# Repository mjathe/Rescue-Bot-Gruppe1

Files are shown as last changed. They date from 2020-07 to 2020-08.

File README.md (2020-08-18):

# Rettungsroboter - Projekt angewandte Elektrotechnik
Wenn Menschen an gefährlichen Orten verunfallen. müssen diese gerettet werden. Manchmal ist die Situation so gefährlich, dass eine erhöhte Gefahr für den Rettenden nicht ausgeschlossen werden kann. In solchen Situation ist es sinnvoll Rettungsroboter einzusetzen.

Im Rahmen dieses Projekts soll ein Rettungsroboter entwickelt werden, welcher sich autonom in einer festgelegten Umgebung bewegen kann.
## Projektmanagement
[Trello](https://trello.com/b/rEBa2gHf/rescue-bot-group-1)

## Szenario
Das Szenario ist ein Waldbrand. Der Roboter wird an einer bestimmten Stelle ausgesetzt und soll sich autonom zu der zu rettenden Person navigieren. Für die Selbstbehandlung der Person, trägt der Roboter ein Erste-Hilfe-Kit mit sich. Außerdem soll bei der Person ein blaues Rauchsignal gezündet werden, damit ein Rettungsteam den Standort bestimmen kann. Für die Kommunikation zwischen Rettungsteam und der Person besitzt der Roboter eine Gegensprechanlage.

## Requirements
| ID |Description  |
|--|--|
|  FR A|Der Roboter muss autonom fahren können.  |
| FR A.1|Der Roboter muss auf dem Land fahren können.|
|NFR A.1.1 | Der Roboter soll auf Ketten fahren.|
|FR A.2|Der Roboter muss auf dem Wasser fahren können.|
|FR A.2.1|Der Roboter muss schwimmen können.|
|FR A.2.2|Der Roboter muss wasserfest sein.|
|NFR A.2.3|An den Ketten befinden sich Paddelbleche für die Bewegung im Wasser.|
|FR A.3|Der Roboter muss Hindernissen ausweichen können.|
|FR A.3.1|Der Roboter muss Hindernisse erkennen.|
|FR B|Der Roboter muss einen Erste-Hilfe-Kasten tragen können.|
|FR C|Der Roboter muss Schallsignale erkennen und differenzieren können.|
|FR C.1|Der Roboter muss Schallsiganle in der Ebene aus allen 4 Richtungen erkennen.|
|FR D|Der Roboter muss das zu retten Objekt identifizieren können.|
|FR D.1|Der Roboter muss die Temperatur des Objekts bestimmen können.|
|FR D.2|Die Temperatur soll über eine Wärmebildkamera bestimmt werden.|
|FR E|Der Roboter soll eine Gegensprechanlage besitzen.|
|FR F|Der Roboter muss sich bei größerer Beladung für den Landweg entscheiden.|

## Kontextdiagramm

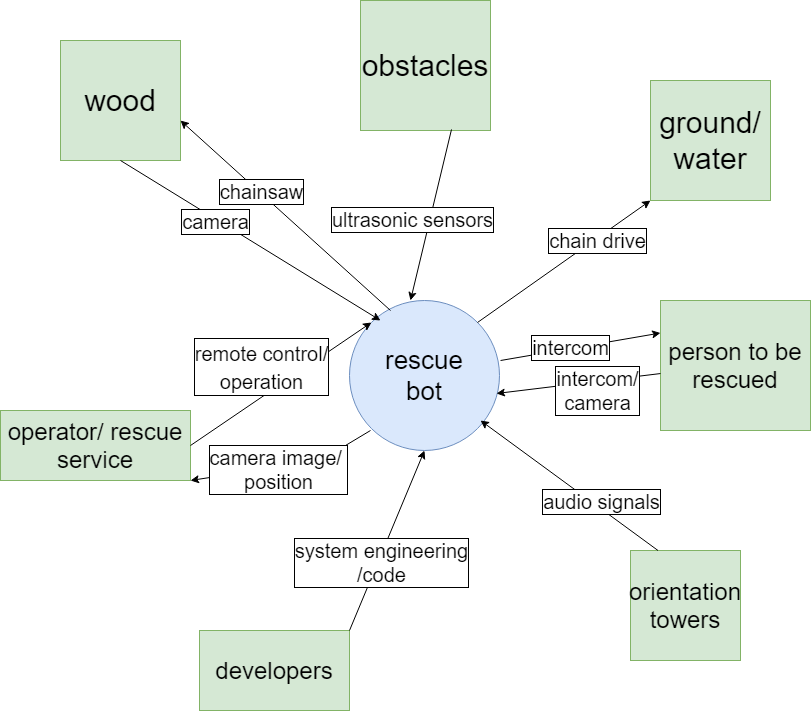
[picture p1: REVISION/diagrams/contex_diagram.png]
Kontextdiagramm


## Use Case Diagram

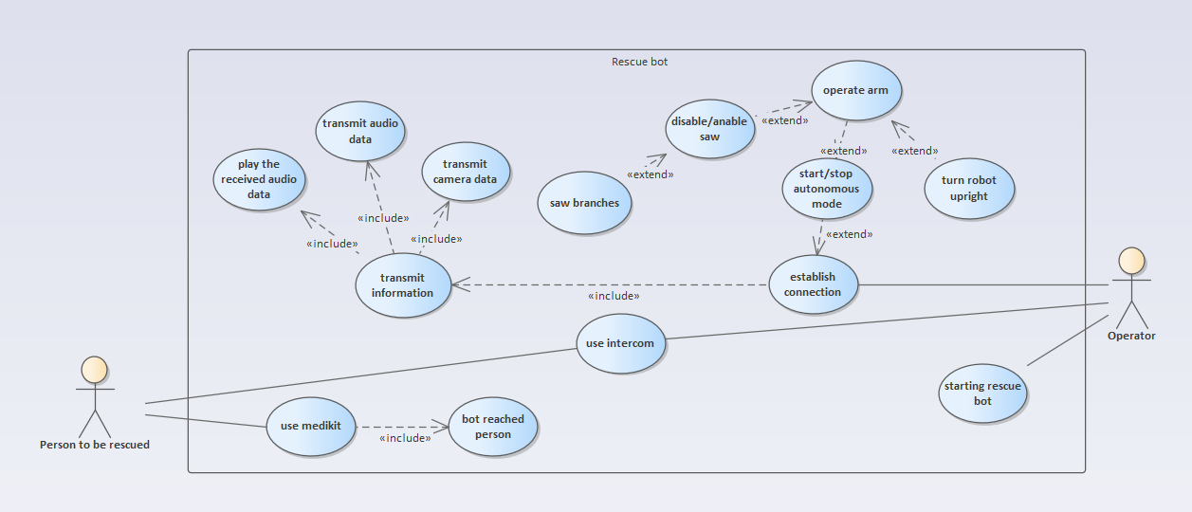
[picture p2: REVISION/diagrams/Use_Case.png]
Use Case Diagram


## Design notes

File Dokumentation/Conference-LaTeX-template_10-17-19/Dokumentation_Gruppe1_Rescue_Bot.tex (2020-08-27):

\documentclass[conference]{IEEEtran}
\IEEEoverridecommandlockouts
% The preceding line is only needed to identify funding in the first footnote. If that is unneeded, please comment it out.
\usepackage{cite}
\usepackage{amsmath,amssymb,amsfonts}
\usepackage{algorithmic}
\usepackage{graphicx}
\usepackage{textcomp}
\usepackage{xcolor}
\def\BibTeX{{\rm B\kern-.05em{\sc i\kern-.025em b}\kern-.08em
    T\kern-.1667em\lower.7ex\hbox{E}\kern-.125emX}}
\begin{document}

\title{Conference Paper Title*\\
{\footnotesize \textsuperscript{*}Note: Sub-titles are not captured in Xplore and
should not be used}
\thanks{Identify applicable funding agency here. If none, delete this.}
}

\author{\IEEEauthorblockN{ Benedikt Lipinski}
\IEEEauthorblockA{\textit{Hochschule Hamm- Lippstadt} \\
Soest,Germany \\
benedikt.lipinski@stud.hshl.de}
\and
\IEEEauthorblockN{ Jonas Gerken}
\IEEEauthorblockA{\textit{dept. name of organization (of Aff.)} \\
\textit{name of organization (of Aff.)}\\
City, Country \\
email address or ORCID}
\and
\IEEEauthorblockN{ Michael Jathe}
\IEEEauthorblockA{\textit{dept. name of organization (of Aff.)} \\
\textit{name of organization (of Aff.)}\\
City, Country \\
email address or ORCID}
\and
\IEEEauthorblockN{ Niklas Heiber}
\IEEEauthorblockA{\textit{dept. name of organization (of Aff.)} \\
\textit{name of organization (of Aff.)}\\
City, Country \\
email address or ORCID}

}

\maketitle

\begin{center}
\begin{abstract}
This document is a model and instructions for \LaTeX.
This and the IEEEtran.cls file define the components of your paper [title, text, heads, etc.]. *CRITICAL: Do Not Use Symbols, Special Characters, Footnotes, 
or Math in Paper Title or Abstract.
\end{abstract}
\end{center}
\titlepage

\section{Motivation (BL)}
In Katastrophenlagen und Ausnahmesituationen können für Menschen oft lebensbedrohliche Bedingungen herrschen. So, dass es im Einsatz von Rettungskräften nicht selten zu gefährlichen Momenten kommt, in denen die eigentlich zur Hilfe eingesetzten Kräfte, selbst zu Hilfe-Ersuchenden werden. \par
Ein Einsatzszenario, in dem Verletzungen, oft schwerwiegend sind, ist die Bedrohung durch Waldbrände. Das Risiko für Einsatzkräfte, sich bei einem Waldbrand zu verletzten, steigt mit jedem brennenden Hektar an Fläche deutlich an. So zeigte sich hier in den letzten 2 Jahren ein starker Anstieg an brennender Fläche mit zuletzt im Jahr 2019 2.711 ha Fläche \cite[S.7B1]{stat1}. Da ein Anstieg an brennender Fläche nicht nur ein erhöhtes Verletzungsrisiko, sondern auch erschwerte Bedingungen an die Einsatzdurchführung selbst stellt. \par
Da der Schutz von Menschenleben und Einsatzkräften an oberste Stelle steht, aber die Bedingungen in einem Waldbrandeinsatz nicht immer den gedankenlosen Einsatz von menschlichem Personal zulassen, sind die rettenden Einheiten auf technische Lösungen angewiesen, die zu ihrem Schutz und ihrer Unterstützung beitragen.\par 
Zur schnelleren Rettung von vermissten Personen und gleichzeitigem Selbstschutz von Einsatzkräften wird ein technisches Gerät benötigt, das verletzte Personen in einem Waldbrandgebiet aufsuchen kann und somit eine Rettung der Person ohne Gefahr für dritte bezweckt. 
Entwickelt werden soll ein Prototyp, der automatisiert und selbständig eine verletzte Person in einer vorgegeben Umgebung aufspüren kann(A). Der Roboter kann sowohl über Land, wie auch über Wasser zu seinem Ziel gelangen(A1,A2), was ihm mittels eines Kettenantriebes ermöglicht wird(A1.1). Damit das Fahren auf dem Wasser möglich ist, werden an den Laufwerken einzelne Kettenglieder zu Paddelblechen geformt (A2.3)
Um sich selbstständig in seiner Umgebung zurechtfinden zu können, muss der Roboter Hindernisse erkennen und ihnen ausweichen können(A3,A3.1).
\par Um sich im Gelände orientieren zu können, navigiert sich der Roboter indem er auf ein spezifisch codiertes Schall-Signal von bis zu 4 Türmen reagieren kann (C, C.1)
In der Interaktion mit einem potentiellen Waldbrandopfer soll das Fahrzeug einen Ersthilfekasten bei sich tragen(B), um der gefundenen Person zu ermöglichen, kleinere Verletzungen bei sich selbst zu behandeln. Zudem sollen Temperaturen von Objekten bestimmt werden können, damit die eines Menschen so wie auch die Temperatur des zu befahrenen Bereichs bestimmt werden kann ( D.1). Des Weiteren kann die verletzte Person mittels einer Gegensprechanlage Kontakt mit dem Rettungspersonal aufnehmen(E). Eine weitere- jedoch verworfene- Anforderung ist die Entscheidung für einen Landweg, sollte das Fahrzeug zu schwer gelastet sein. Jedoch sind im Projektverlauf weitere Anforderungen hinzu gekommen, zum Beispiel wäre das die Umsetzung einer vom Operator per Fernbedienung gesteuerten Kettensäge auf dem Roboter. Diese Funktion soll eine bessere Fortbewegung im Gelände ermöglichen.
\par Die Anforderungen wurden durch die komplette Gruppe anhand des durch die Aufgabe festgelegten Rahmens erstellt.

\begin{figure}[h] 
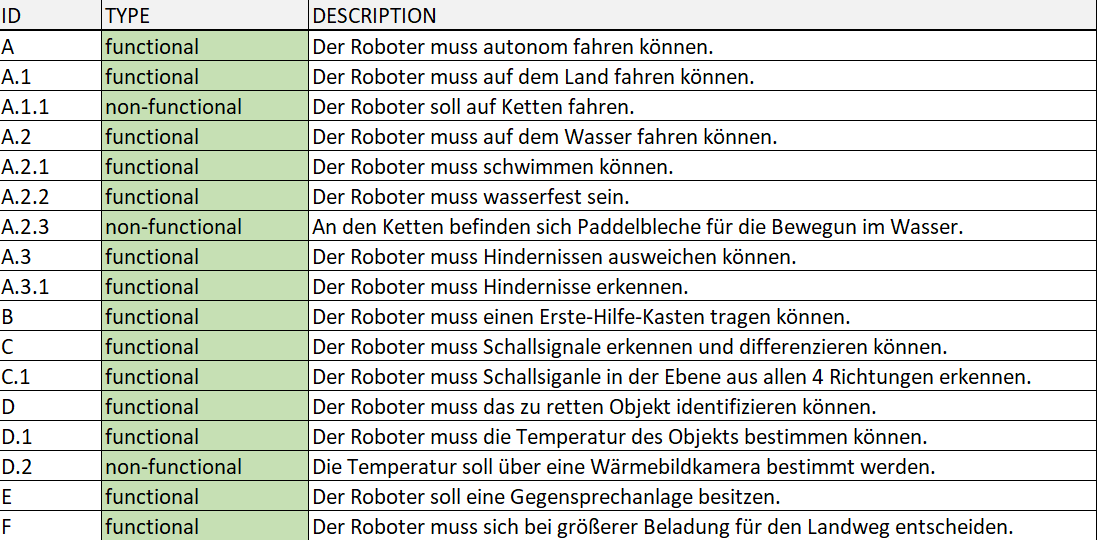
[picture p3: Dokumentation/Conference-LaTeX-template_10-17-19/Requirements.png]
\center{}
\caption{Anforderungsliste }
\label{fig.1}
\end{figure}

\section{Implementation des Roboters (BL)}
{
Als letzten Schritt vor der finalen Umsetzung in wirklichen Programmiercode wurden die abgeleiteten Algorithmen beispielhaft ohne jegliche reale Syntax Umgesetzt. Die diente zum besseren Verständnis der späteren Übersetzung der Algorithmen von der Beschreibung durch Diagramme in die Beschreibung durch von Maschinen lesbare Sprache. Ziel war es zudem, nicht nur einem Compiler die Lesbarkeit zu ermöglichen, sondern auch die Abstimmung in der Gruppe, um zu gewährleisten, dass der durch mich abgeleitete Code, auch den übrigen Gruppenmitgliedern in der Form schlüssig erschien und nicht durch ein Verständnisproblem in eine falsche Richtung entwickelt wurde. Ein positiver Nebeneffekt ist zudem, dass sich bereits nach der Umsetzung in Pseudo-Code mögliche Unstimmigkeiten in Schnittstellen aufgetan hätten, aber auch die Arbeit von mehr als einer Person in der weiteren Umsetzung nicht die Gefahr gebracht hätte, Fehler zu erzeugen. \par
Die Entscheidung, in welcher Programmiersprache der Roboter umgesetzt wird, fiel auf C++. Die Gründe für die Auswahl ergeben sich daraus, dass Programme in C++ leicht zu verstehen und auch umzusetzen sind. Das bedeutet, die Programmierung war für alle Teilnehmer in der Gruppe ohne Probleme möglich, da bereits im Verlauf des Studiums alle Mitglieder mehrfach durch die Arduino-Programmierung im Rahmen von Projekten zu tun hatten und somit nicht erst eine neue Sprache zu erlernen hatten. Weitere Vorteile von C++ sind, dass die Sprache in ihrem Kern recht schlank ist, und somit sehr schlank ist. Auf Funktionen muss allerdings nicht verzichtet werden, da eine große Anzahl an Bibliotheken zur Verfügung steht, die bei Bedarf mit eingebunden werden können. Letzter Entscheidungsgrund für C++ ist der Schlankheit der Sprache geschuldet. Entscheidend war der Faktor, dass C++ auf einer hohen Anzahl an Umgebungen zur Verfügung steht. Beispiele wären der bereits erwähnte Arduino, der sich besonders für das Entwickeln von Prototypen eignet. Ein weiteres Beispiel sind Microsoft Windows Betriebssysteme, in denen mit einem C++ Compiler und den Entwicklungsumgebungen von zum Beispiel  Visual Studio oder Eclipse sehr komfortabel Quellcode in C++ entwickelt werden kann.\par 
Zu den aktuellen Bestandteilen des Systems, die in Programmiercode umgesetzt wurden, zählen die elementaren Bestandteile der selbständigen Fahrt zu einer verunfallten Person in einem Testszenario. Genauer wurde die Entscheidung umgesetzt, ob ein Fahrzeug sich zum Zeitpunkt auf dem Landweg, oder auf dem Wasser befindet. Des weiteren wurde Wert auf die Navigation per Schallsendeturm gelegt und implementiert. Der Prototyp kann zudem voll automatisch auf die Türme ausrichten und die Motoren ansteuern. Zu diesem Zeitpunkt wurde die folgende Liste an Klassen implementiert: 

Alignment.hpp, in der die Ausrichtung des Fahrzeugs auf Basis der Navigationsdaten der AudioNavigation in Grad eingestellt wird. Dementsprechend wird in der AudioNavigation.hpp Steueranweisung für das Ausrichten berechnet. Für diesen Schritt müssen Informationen von den Audiosendetürmen vorliegen. 
Die Entscheidung ob sich das Fahrzeug im Wassermodus bewegt, oder ob der Landmodus festgelegt ist, wird im DriveMode.hpp eingestellt. Aufgerufen werden diese Klassen durch die MainControl.hpp fortlaufen, solange bis ein Operator die autonome Fahrweise des Roboters unterbrechen sollte. Des weiteren wird die Umgebung des Fahrzeugs auf Hindernisse überprüft, was mittels ObjectDetection.hpp implementiert wurde.
Nach einem positiven Befund der ObjectDetection.hpp wird aufgrund der festgelegten Requirements des Projektes noch ein weiterer Schritt notwendig, der in der ObstacleDetection.hpp zum jetzigen Zeitpunkt( 26.08.2020) nur angedeutet wurde. Bei diesem schritt handelt es sich um die Unterscheidung eines nicht näher bekannten Objekts, in dem Falle ein Hindernisse, oder der Entscheidung zwischen einem der beiden bekannten Objekte, die sich aus der Kategorie Äste und der Kategorie Personen ergeben.

Zudem wurde die Kommunikation mit den Sensoren über die SensorController.hpp umgesetzt, aber auch die Ansteuerung des Laufwerksmotors wurde mit der MotorControl.hpp implementiert
\par
Als sehr wichtigen Bestandteil des Projektes stellt sich die Implementation der AudioNavigation heraus, die im Folgenden genauer beschrieben wird.
\par
\textit{Alignment.hpp}\\
Damit eine zuverlässige Navigation durch die Testumgebung stattfinden kann ist es für das Fahrzeug notwendig, die Richtung in die der Roboter zu fahren hat herausfinden kann, dazu benötigt er eine kleine Hilfestellungen durch auf dem Gelände montierte Schallsignal gebende Türme, deren Position bekannt ist.
Durch diese Navigationshilfe und die Bekanntheit der Strecken kann das Fahrzeug entscheiden, wie es sich zu verhalten hat.
\par 
In der Erweiterung, die die Alignment.hpp dem Roboter zur Verfügung stellt, kann der Rescue-Roboter sich basierend auf dem Nordpol der Karte und seiner eigenen Differenz dazu ermitteln, um wie viel Grad er sich drehen muss, um in Richtung des Sendeturms ausgerichtet zu sein. Hierbei hilft ihm die Codierung des Turms und die Differenz der Ausrichtung, die mittels Signalen eines Kompass ermittelt werden kann. Implementiert ist dies durch zwei Klassen mit einer steuernden Funktion: \textcolor{teal}{adjustAlignment} deren Aufgabe darin besteht zum einen, die Rechnung zu Differezberechnung \textcolor{teal}{differenceAlignment} aufzurufen, und zum zweiten das Ergebnis an die Motoren weiter zu geben. Die Formel für die Differenz wird errechnet aus der $differenz =gewünschtenAusrichtung - aktuellenAusrichtung $. Die gewünschte Ausrichtung wird durch den Aufruf aus der Klasse  AudioNavigation mit übergeben.\par
\par
\textit{AudioNavigation.hpp}
\par
Genauer wird die gewünschte Ausrichtung in der Methode \textcolor{teal}{Navigate} der Klasse AudiNavigation festgelegt. Basierend auf der Information welcher Turm ein positives Signal gegeben hat, kann in der Navigationsklasse entschieden werden in welche Richtung sich gedreht werden soll. 
Dazu ist bekannt, bei welcher Kombination von aktiven Türmen sich in welche Richtung gedreht werden muss. Ein Beispiel dazu: sollte  $checkForAudioSignals() = {1,0,0,1}$ zurück geben, dann kann das Fahrzeug sich nur am Umkehrpunkt befinden. Die eingestellte Richtung wäre in diesem Fall 90° im Verhältnis zum Nordpol der Karte, das Fahrzeug würde Richtung Osten fahren-  auf Turm 4 zu. Der Grund für die Entscheidung besteht darin, dass die strecke vom Start bis zum Turm 4 die kürzeste Strecke zum Patienten ist. 
\par
\textit{SensorController.hpp}
\par
Die für die Streckenwahl notwendigen Informationen lassen sich aus der für den SensorController bestimmten Klasse SensorController abrufen. Die in dem SensorController überwiegend erledigten Aufgaben beziehen sich zu einem sehr großen Teil darauf, Informationen von Sensoren zu erfragen und diese bereits vor der eigentlichen Verarbeitung aufzubereiten. Die Aufbereitung bedeutet zum Beispiel, dass im Falle der Navigation mittels Schall eine Codierung des Schallsignals zur Bestimmung des Startpunktes der Nachricht vor der eigentlichen Nachricht übermittelt wird. Ganz konkret bedeutet das, dass die Nachricht die den Turm 1 beschreibt nicht nur aus $001$, sondern aus jeweils drei vorangestellten HIGH und LOW Bits besteht, demnach $111000001$. Die Informationen ob und welcher Turm erkannt wurde, werden nur in dem Fall zurückgegeben, wenn diese Codierung korrekt abgeglichen werden konnte.
Des weiteren behandelt der Sensorcontroller die Abfrage der Ultraschallsensoren, der Wassersensoren und des Kompass. Zusammenfassend lässt sich sagen, dass der SensorController einen großen Teil der Schnittstellen mit denen der Rescue-Bot mit seiner Testumgebung interagiert beinhaltet. 
\par

||Die Klasse SensorController.hpp wurde durch "mich" auf der Grundlage von der durch Jonas Gerken erstellten ersten Implementierung des SensorControllers verfeinert. Die weiteren Klassen mit denen das Verhalten des Rescue-Bots umgesetzt wurde, sind zusammengerechnet ca. 30h Zeit. ||
\par 

Die Umsetzung des Projektes beinhaltet, neben der Implementierung eines Rettungsroboters, auch die Simulation einer Umgebung in der sich der Roboter bewegen soll. Das beinhaltet neben der Umgebung selbst auch die Interaktion mit dieser simulierten Umgebung.

}

\begin{IEEEkeywords}
component, formatting, style, styling, insert
\end{IEEEkeywords}
\bibitem{stat1} Bundesanstalt für Landwirtschaft und Ernährung,Waldbrandstatistik der Bundesrepublik Deutschland für das Jahr 2019, Statista,Veröffentlichung 25.06.2020, Waldbrand statistik-b.pdf, Letzter Abruf 25.08.2020

\begin{thebibliography}{00}

\end{thebibliography}
\vspace{12pt}
\end{document}

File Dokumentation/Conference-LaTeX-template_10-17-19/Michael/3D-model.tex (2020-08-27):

\begin{figure}[h]
    \centering
    \captionsetup{width=.9\linewidth}
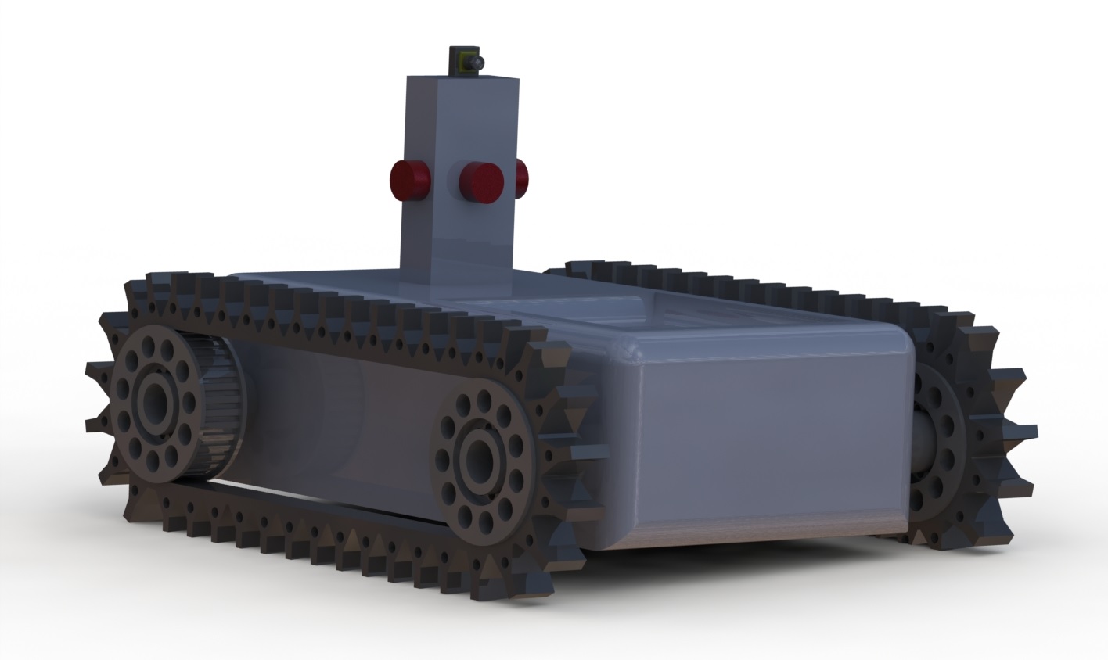
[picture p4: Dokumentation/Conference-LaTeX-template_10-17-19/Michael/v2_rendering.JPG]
    
    \caption{Erster Prototyp}
    \label{fig:prot}
\end{figure}

Das 3D-Modell des Rettungsroboters wurde mit der Software SolidWorks erstellt. Die Abbildung \ref{fig:prot} zeigt den ersten Prototyp. Hier wurden schon der Kettenantrieb und eine Ablagefläche für ein Erste-Hilfe-Kit umgesetzt. Weiter wurde auf dem Robotor ein Turm platziert, um dort 4 Sensroen für die Orientierung anzubringen. Oben auf dem Turm befindet sich eine Kamera.\\

\begin{figure}[h]
    \centering
    \captionsetup{width=.9\linewidth}
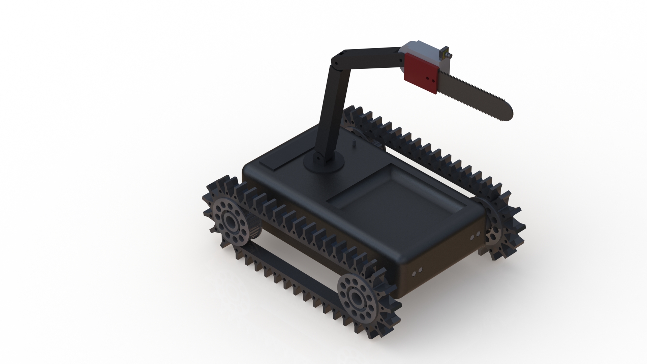
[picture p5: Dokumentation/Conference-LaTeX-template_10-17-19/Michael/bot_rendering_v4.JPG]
    
    \caption{Zweite Version des Roboters}
    \label{fig:second}
\end{figure}

Für die zweite Version des Prototyps wurde zunächst der Körper des Bots angepasst. Für eine Verbesserung des Strömungsverhaltens und einer Erhöhung des Böschungswinkels wurde der Körper an der vorderen unteren Kante mit einer sehr flachen Fase versehen.

Im nächsten Schritt wurde der unbewegliche Turm durch einen Roboterarm mit 3 Gelenken und einer Drehscheibe ersetzt (Abb. \ref{fig:second}). Am Ende des Arms wurde eine Kettensäge angebracht. Die Kamera wurde auf der Säge angebracht, um so die Säge immer im Blick zu haben.

Weiter wurden noch ein austauschbarer Akku, ein omnidirektionales Mikrofon und Ultraschallsensoren in den Prototyp intgeriert.\\
\begin{figure}[h]
    \centering
    \captionsetup{width=.9\linewidth}
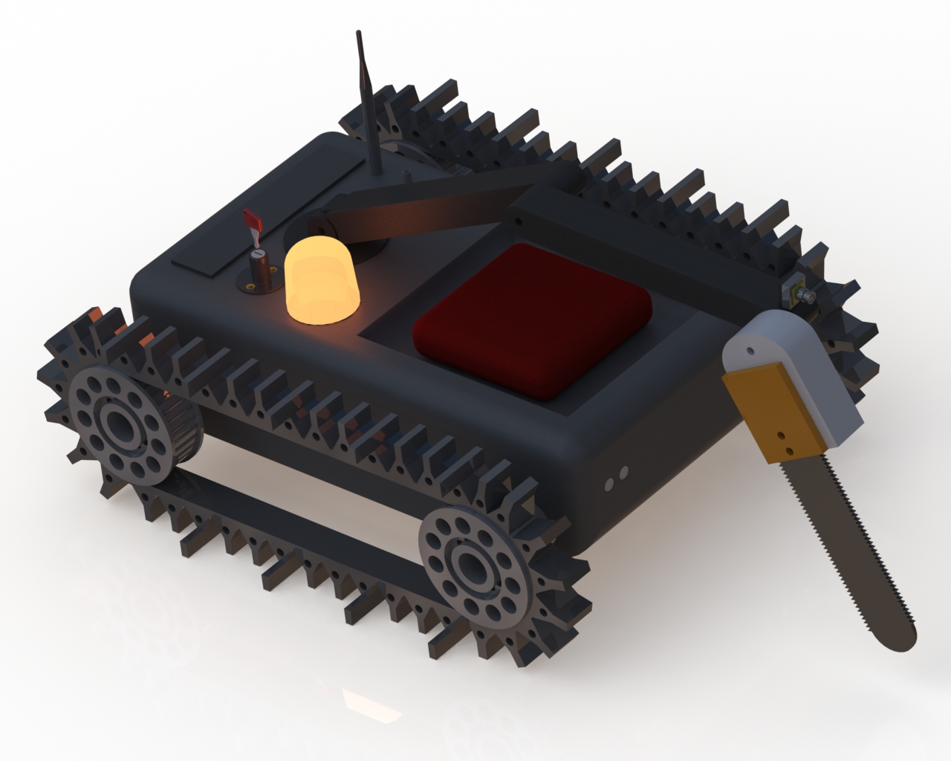
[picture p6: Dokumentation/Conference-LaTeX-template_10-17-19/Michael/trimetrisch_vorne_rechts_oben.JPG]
    
    \caption{Außenansicht des finalen Roboters}
    \label{fig:final}
\end{figure}
Abbildung \ref{fig:context} zeigt das finale Modell. Im Vergleich  zur vorherigen Version noch folgende Elemente hinzugefügt:
\begin{itemize}
    \item Rundumleuchte
    \item Antenne
    \item Ein/Aus-Schalter
    \item seitliche Paddel an den Ketten\\
\end{itemize}

Der komplette Arm des Roboters hat eine Revision erfahren, so dass die beiden Teilarme und die Säge eingeklappt werden können. Die Kamera wurde auf den oberen Arm versetzt, damit die Kettensäge eingeklappt werden kann und der Operator trotzdem die Sicht nach Vorn behält.

Außerdem wurde der Hauptkörper des Roboters in eine Wanne und einen Deckel unterteilt, um zum Einen die Teile druckbar zu machen und zum ist nur so möglich die benötigte Hardware (Motoren, Mikrocontroller, usw.) zu installieren.  \\

Die Abbildungen \ref{fig:top} und \ref{fig:front} zeigen, dass für die vorgesehene Hardware genug Platz vorhanden ist und auch entsprechende Befestigungspunkte vorhanden sind.\\
\begin{figure}[h]
    \centering
    \captionsetup{width=.9\linewidth}
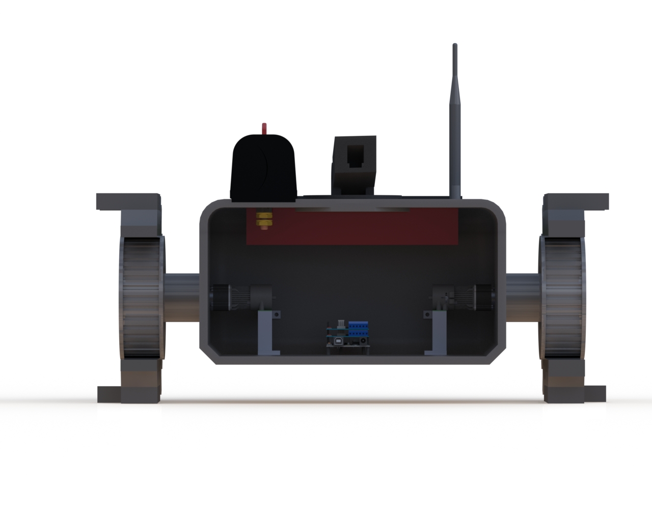
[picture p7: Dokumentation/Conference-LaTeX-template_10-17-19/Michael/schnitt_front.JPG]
    
    \caption{Schnittansicht von vorne}
    \label{fig:front}
\end{figure}\\
\begin{figure}[h]
    \centering
    \captionsetup{width=.9\linewidth}
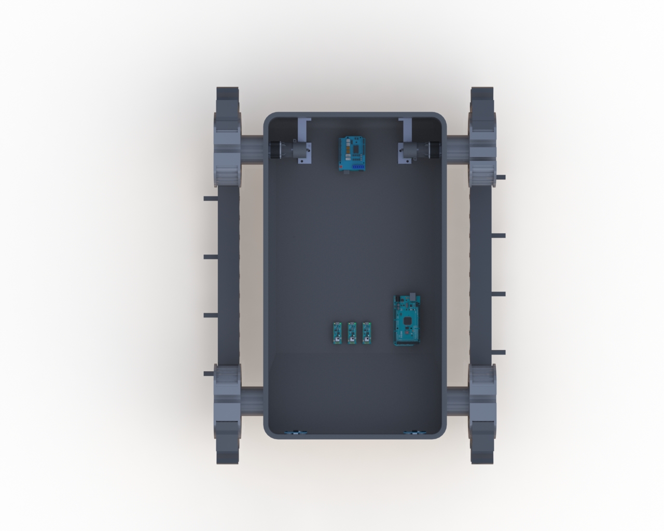
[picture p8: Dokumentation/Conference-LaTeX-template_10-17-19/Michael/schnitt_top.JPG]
    
    \caption{Schnittansicht von oben}
    \label{fig:top}
\end{figure}\\
Zum Schluss wurden alle Druckteile mit Hilfe des Felix Repetier Hosts auf Druckbarkeit überprüft. Abbildung \ref{fig:print_stats} zeigt die Statistiken für einen 3D-Druck mit 25\% Infill  und ABS Filament. Aus der benötigten Filamentmenge und der spezifischen Materialdichte lässt sich das Gewicht der Druckteile errechnen (Abb. \ref{fig:filament_weight}). Hier ergibt sich ein Gewicht von etwa 5,67 kg.

In Solidworks wurde für die Wanne des Hauptkörpers ein Volumen von etwa 7,9 Liter berechnet. Daraus lässt sich schließen, dass der Roboter ein Gesamtgewicht von 7,9 kg nicht überschreiten sollte. Da die Druckteile schon 5,67 kg  wiegen, bleiben für die restlichen Teile (Motoren, Akku, Elektronik, Säge, Lager, Erste-Hilfe-Kit) nur etwa 2,23 kg.
Das wäre nicht sinngemäß zu realisieren. Das bedeutet der Hauptkörper sollte noch deutlich vergrößert werden. Zusätzlich könnten die Wandstärken verringert werden, um Gewicht zu Sparen. Für die Teile des Roboterarms würde sich ein Fachwerk anbieten. 
\begin{figure}[h]
    \centering
    \captionsetup{width=.9\linewidth}
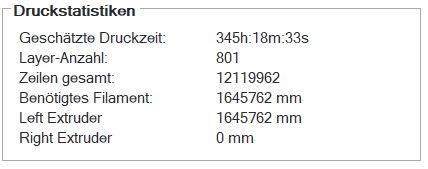
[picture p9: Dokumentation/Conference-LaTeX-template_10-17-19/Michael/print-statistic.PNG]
    
    \caption{Druckstatistiken}
    \label{fig:print_stats}
\end{figure}
\begin{figure}[h]
    \centering
    \captionsetup{width=.9\linewidth}
    
    \caption{Erechnetes Filamentgewicht}
    \label{fig:filament_weight}
\end{figure}

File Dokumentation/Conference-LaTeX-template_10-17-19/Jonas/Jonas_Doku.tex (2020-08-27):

\documentclass[conference]{IEEEtran}
\IEEEoverridecommandlockouts
% The preceding line is only needed to identify funding in the first footnote. If that is unneeded, please comment it out.
\usepackage{cite}
\usepackage{amsmath,amssymb,amsfonts}
\usepackage{algorithmic}
\usepackage{graphicx}
\usepackage{textcomp}
\usepackage{xcolor}
\def\BibTeX{{\rm B\kern-.05em{\sc i\kern-.025em b}\kern-.08em
    T\kern-.1667em\lower.7ex\hbox{E}\kern-.125emX}}
\begin{document}

\title{PAE Gruppe 1*\\
{\footnotesize \textsuperscript{*}Note: Sub-titles are not captured in Xplore and
should not be used}
\thanks{Identify applicable funding agency here. If none, delete this.}
}

\author{\IEEEauthorblockN{1\textsuperscript{st} Given Name Surname}
\IEEEauthorblockA{\textit{dept. name of organization (of Aff.)} \\
\textit{name of organization (of Aff.)}\\
City, Country \\
email address or ORCID}
\and
\IEEEauthorblockN{2\textsuperscript{nd} Given Name Surname}
\IEEEauthorblockA{\textit{dept. name of organization (of Aff.)} \\
\textit{name of organization (of Aff.)}\\
City, Country \\
email address or ORCID}
\and
\IEEEauthorblockN{3\textsuperscript{rd} Given Name Surname}
\IEEEauthorblockA{\textit{dept. name of organization (of Aff.)} \\
\textit{name of organization (of Aff.)}\\
City, Country \\
email address or ORCID}
\and
\IEEEauthorblockN{4\textsuperscript{th} Given Name Surname}
\IEEEauthorblockA{\textit{dept. name of organization (of Aff.)} \\
\textit{name of organization (of Aff.)}\\
City, Country \\
email address or ORCID}
}

\maketitle

\begin{abstract}

\end{abstract}

\section{Use Case (JG)}

\begin{figure}[htbp]
	\centering
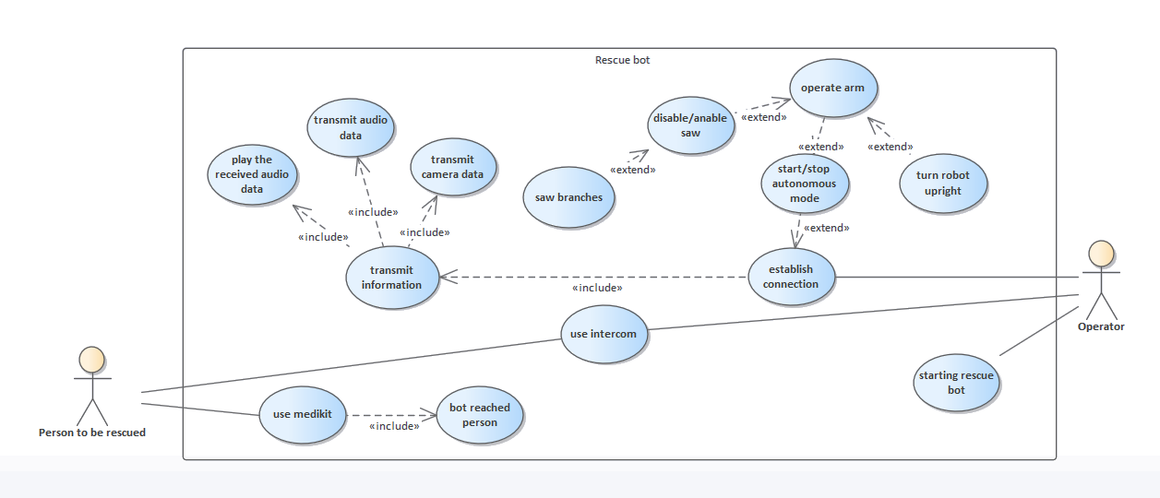
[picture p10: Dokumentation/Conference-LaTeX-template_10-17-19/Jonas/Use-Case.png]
	
	\caption{Use Case}
\end{figure}

Nach der Erstellung der Anforderungen haben wir ein Use Case Diagramm erstellt.\newline 
In Fig. 1 ist das Use Case Diagramm zusehen. Außerhalb stehen die Aktoren "Operator" und "Person to be rescued", als Strichmännchen dargestellt. Innerhalb sind die Funktionen des rescue bots dargestellt und wie diese mit den Aktoren verbunden sind. Die Use Cases sind mit inludes oder extends untereinander verbunden. Die Aktoren sind durch Assoziationen mit den Use Cases verbunden. Zum Beispiel kann der Operator den rescue bot starten. Dann stellt der Operator eine Verbindung mit dem rescue bot her. Über die Verbindung zum rescue bot werden verschiedene Informationen, wie Kamera Daten und Audio Daten übermittelt. Der Operator kann zwischen Autonomen und manuellen Modus wechseln. Im manuellen Modus kann der Operator den Arm bedienen. Zudem kann er eine Säge aktivieren oder deaktivieren um Äste zu durchsägen.
Der Arm kann auch dafür benutzt werden, den rescue bot wieder aufzustellen wenn er auf die Seite gefallen ist.
Wenn der rescue bot die zu rettende Person erreicht hat, kann der Operator über eine Gegensprechanlage die Person ansprechen. Zum schluss kann die zu rettende Person ein medikit benutzen, um selbst kleine Verletzungen zu versorgen.

\section{Stakeholder (JG)}
Um mögliche Risiken oder Blockaden, die das Projekt stoppen oder zum Abbruch bringen können zu finden haben wir eine Stakeholderanalyse durchgeführt. Stakeholder sind alle Personen, die mit dem Projekt in Kontakt kommen. Dazu gehören z.B. der Arbeitgeber, das Rettungsteam, die zu rettende Person (Opfer), Finanzmanager und der TÜV.
\\

\subsection{Rettungshelfer}
Die Rettungshelfer wollen sich selbst und dritte nicht zusätzlich in gefährlichen Situationen in Gefahr bringen.
Die Lösung dafür ist, das der Roboter anwendbar für Situationen die zu Gefährlich für die Rettungshelfer sind gemacht wird.

\subsection{Menschen die gerettet werden}

Die zu rettenden Menschen wollen eine schnelle medizinische Hilfe und schnelle Rettung.
Hier ist die Lösung, das der zu rettende Mensch so schnell und sanft wie möglich gerettet wird.

\subsection{Familie des zu rettenden Menschen}

Die Familie des zu rettenden Menschen will wissen, das ihre Verwandtschaft in Sicherheit ist.
Um der Familie dies zu bieten, muss dem zu rettenden Menschen die best mögliche Rettung geliefert werden.

\subsection{Finanzmanager}

Der Finazminister will ein Produkt mit einem hohen Mehrwert zu möglichst niedrigen kosten.
Dazu ist die Lösung, ein System mit einem guten Preis-Leistungsverhältnis zu entwickeln.

\subsection{Arbeitgeber}

Der Arbeitgeber möchte ein verkaufbares Prokdut mit einer hohen verkaufsrate und einem hohen Profit.
Die Lösung ist, eine System mit hoher Sicherheit aufzubauen, um eine Entschädigung zu vermeiden und einen Kaufanreiz zu schaffen, der auch mit einem hohen Profit möglich ist.

\subsection{TÜV}

Der TÜV möchte Sicherheit für alle Beteiligten, wie Rettungshelfer, Menschen die gerettet werden sollen und Dritte.
Um dies einzuhalten müssen Richtlinien eingehalten und ein sicheres System eingerichtet werden, um eine TÜV-Zertifizierung zu bekommen. 

\subsection{Kunden}

Der Kunde will, das die Rettungshelfer gut ausgestattet sind.
Dazu wird der rescue bot(Ausstattung) in regelmäßigen abständen gewartet. Zudem gibt es eine Kundenbetreuungen um sie mit dem neuen Produkt vertraut zu machen. Dies ist wichtig um mögliche bedenken zu dem rescue bot beiseite zu schaffen.
\\

\subsection{Stakeholder matrix}

\begin{figure}[htbp]
	\centering
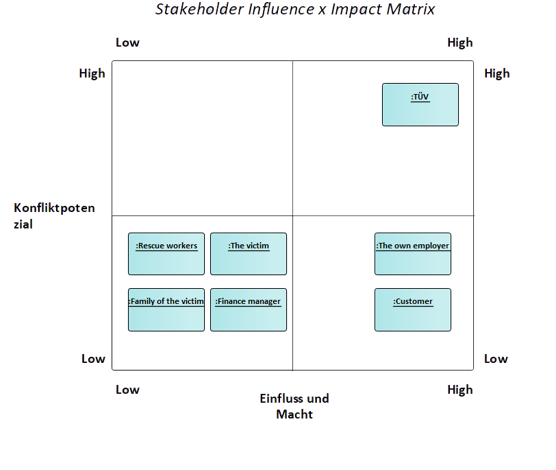
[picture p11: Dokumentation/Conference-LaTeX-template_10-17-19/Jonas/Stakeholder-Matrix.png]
	
	\caption{Stakeholder-Matrix}
\end{figure}

In Fig. 2 ist die Stakeholder-Matrix mit den verschiedenen Stakeholdern zusehen. Die Stakeholder haben wir nach "Einfluss und Macht" und Konfliktpotential sortiert. Die Rettungshelfer, die zu rettende Person, die Familie der zu rettenden Person und der Finanzmanager haben am wenigsten Einfluss und Macht und am wenigsten Konfliktpotenzial in dem Projekt. Diese Stakeholder können kaum bis gar nichts in dem Projekt mit entscheiden. Zum Beispiel will der Finanzmanager ein Produkt mit einem guten Preis-Leistungsverhältnis wie in Kapitel D beschrieben. Was das Projekt am Ende kostet kann der Finanzmanager jedoch nicht beeinflussen. Viel Einfluss aber wenig Konfliktpotential hat der Arbeitgeber und der Kunde. Zum Beispiel kann der Arbeitgeber viel mit entscheiden, was gemacht werden kann und was nicht. Zudem hat der Kunde eine Vorstellung von dem was er will und kann so starken Einfluss auf das Projekt haben. Der TÜV hat ein hohes Konfliktpotenzial und viel Einfluss und Macht. Durch z.B. fehlenden Sicherheitsmaßnahmen kann der TÜV das Projekt zum Abbruch bringen. 

\section{Activity Diagramm (JG)}

Nachdem das Use Case Diagramm erstellt wurde, haben wir ein Aktivitätsdiagramm bezüglich des autonomen Fahrens, wie in Fig. 3 gezeigt, erstellt. Die erste Aktivität ist, das der Operator sich mit dem Rescue bot über das Remotecontroll und dem remote verbindet. Weiter geht es mit der Sensorauslesung und der Evaluierung der Sensordaten. Darüber überprüft er auf Wasser und entscheidet sich bei "water" für über Wasser fahren und bei "no water" für über Land fahren. Die nächste Aktivität ist, das auf Audiosignale überprüft wird. Bei erkanntem Signal folgt der rescue bot dem Signal, ansonsten fährt er gerade aus weiter. Parallel dazu wird die camera über das remote controll aktiviert. Dazu gehören die Aktivitäten send data, receive data und display video. Wenn ein object erkannt wird, wird das Objekt Identifiziert. Ein Objekt wird unterschieden zwischen nicht identifizierbar, identifiziert als sägbares Objekt und identifiziert als Person. Bei einem zersägbaren Objekt wird nachgefragt ob der rescue bot im Autonomen modus ist. Ist der bot nicht im autonomen Modus, wird der bot gestoppt und der remotecontroll (arm/säge) kann verwendet werden. Danach wird abgefragt ob der bot wartet. Wenn ja, dann wird dem rescue bot erlaubt weiter zu fahren. Sollte das Objekt nicht identifizierbar sein, wird es einfach umfahren. Wurde die Person identifiziert, wird abgefragt ob die Person erreicht wurde. Über jeden weg wird abgefragt, ob die Person erreicht wurde. Also nach der Hindernisumfahrung, dem Äste zersägen. Wurde die Person nicht erreicht, werden die Sensoren wieder ausgelesen und so weiter. Wenn sie erreicht wurde, stoppt der rescue bot und der Operator kann mit der Person reden. Zum Schluss fährt der rescue bot zurück.

\begin{figure}[htbp]
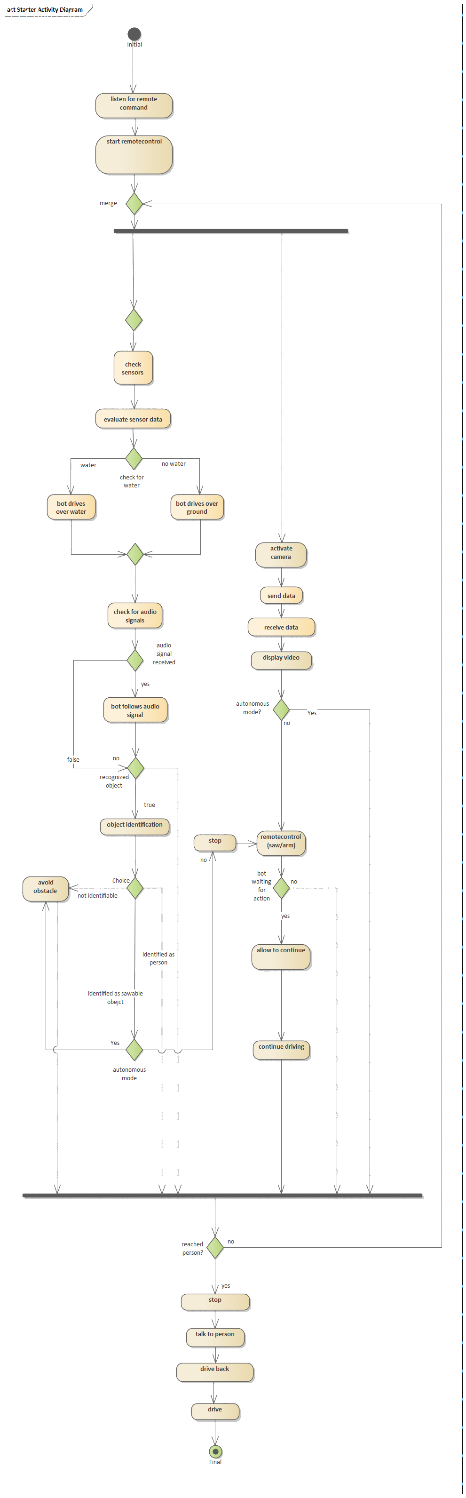
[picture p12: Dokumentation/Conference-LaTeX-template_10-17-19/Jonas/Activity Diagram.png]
	
	\caption{}
	\label{fig:Bild1}
\end{figure}

\newpage

\section{Swimlane (JG)}

In Fig. 4 ist das "Swimlane diagramm" zusehen. Hier wurden die verschiedenen Aktivitäten aus dem Aktivitätsdiagramms nach Sensorcontroller (Blau), Hauptcontroller (Gelb), Motorcontroller (Lila), Objekterkennung (Grün), Remotecontrol (Orange) und remote (Rot) Kategorisiert. Es ist notwendig den rescue bot mit dem remote zu verbinden. Erst danach kann der rescue bot losfahren und die Sensoren auslesen.
Der Sensorcontroller ließt die Sensoren aus und der Hauptcontroller evaluiert sie. Über diese Informationen wird der Motorcontroller angesteuert, ob er auf Land oder Wasser fahren soll. Weiter gibt der Hauptcontroller über empfangene Audiosignale den Befehl, das der rescue bot dem Signal folgen soll. In der Kategorie Objekterkennung unter Objekt Identifizierung wird zwischen nicht identifizierbar, identifiziert als sägbares Objekt und identifiziert als Person unterschieden. Bei einem als zersägbares Objekt identifiziertes Objekt, werden über den Motorcontroller die Motoren gestoppt und der Operator kann über das remote die äste durchsägen. Danach erlaubt der Operator dem rescue bot über die remotesteuerung das weiterfahren. Nachdem die zu rettende Person erreicht wurde, bekommt der Motorcontroller das Signal, die Motoren anzuhalten. Der Operator kann nun über das remote und der Gegensprechanlage mit der zu rettenden Person reden. Am Ende fährt der rescue bot zurück zum Startpunkt.  

\begin{figure}[htbp]
	\centering
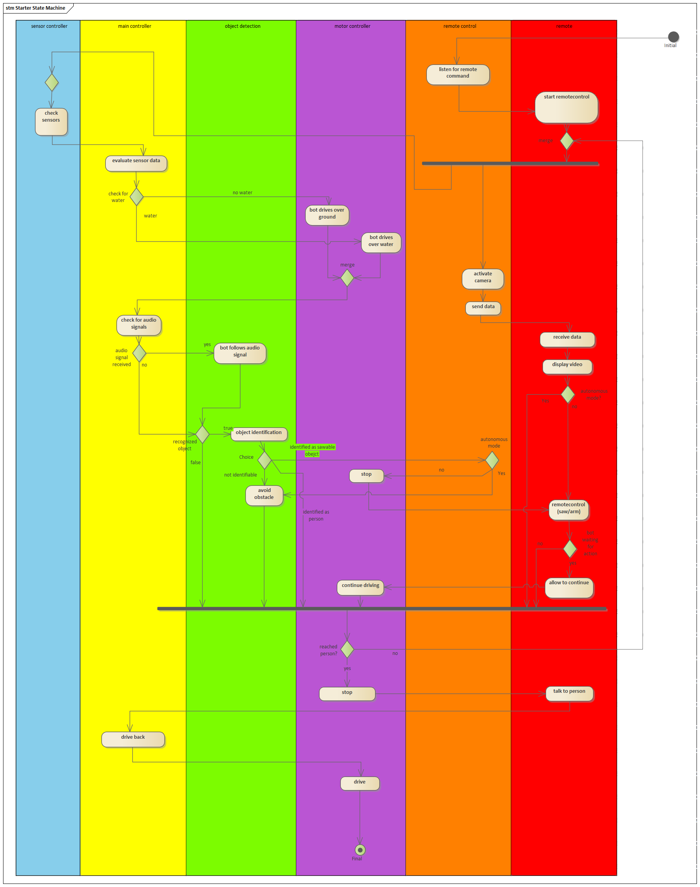
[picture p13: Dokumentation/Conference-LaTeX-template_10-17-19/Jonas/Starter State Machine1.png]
	
	\caption{Swimlane}
	
\end{figure}

\section*{References}

\vspace{12pt}
\color{red}

\end{document}

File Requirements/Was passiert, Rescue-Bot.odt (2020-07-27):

Was passiert, wenn das Feuer bedrohlich wird für Fahrzeug und Objekt ? ?

Es wird ein sprüh-nebel Schutzschild ausgestoßen (ähnl. „Mannschutz“)

Was passiert, wenn die Person eingeklemmt ist ?
aufgrund der Vielfalt der Gegenstände unter denen man eingeklemmt sein könnte stößt das Fahrzeug hier an sein grenzen

Was passiert, wenn der Fluchtweg abgeschnitten ist ?

Das Fahrzeug sucht sich einen anderen weg

Was passiert, wenn das Fahrzeug auf das Dach kippt ?

Durch den (Kettensägen) arm kann das Fahrzeug aufgerichtet werden

Was passiert, wenn das Fahrzeug einen weg um ein Hindernis nicht finden kann ( z.b lange äste ) ?

Das Fahrzeug verfügt über eine kleine Kettensäge

Was passiert, wenn die schleiftrage sich verkantet ?

????? das Fahrzeug setzt andere ende der schleiftrage und versucht sich zu befreien

Was passiert, wenn der Gesundheitszustand der Person sich nicht stabilisiert

?? evtl. per TIVITA wund Erkennung und Hämostatisches mittel

Evtl. Vakuum Matratze mit Beschichter Gold Folie

Ansonsten wenn sich der Zustand nicht verbessert „sofort-Rettung „

Was passiert, wenn die Person zu dick ist um über Wasser zu fahren ?

Der Roboter nimmt den Landweg

- Wenn Fluchtweg abgeschnitten Rettung übers Wasser an Ufernähe ( bestmögliche )

Was passiert, wenn der Roboter bei der Person angekommen ist ?

Per Sprechfunk wird versucht über Kontakter mit der Person in Notlage zu reden

Motor ??
Elektro
DIESEL
Benzin
2Takt

4Takt

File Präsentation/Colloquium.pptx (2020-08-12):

## Colloquium

Gruppe1
Niklas Heiber, Michael Jathe, Jonas Gerken, Benedikt Lipinski

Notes: Benedikt

## Motivation

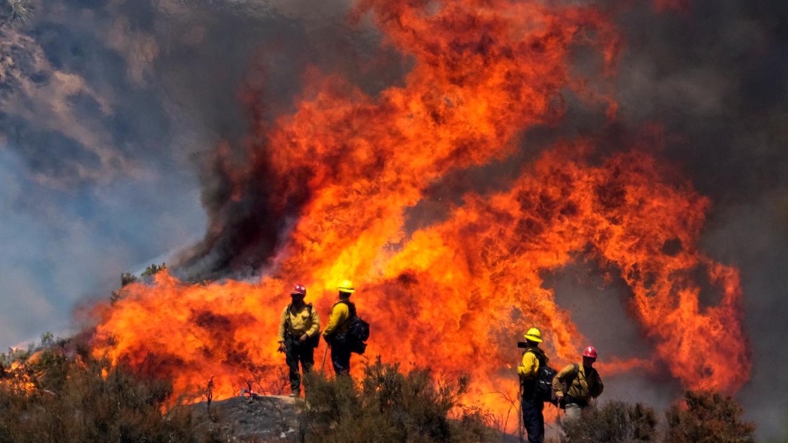
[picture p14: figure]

Einsatz des Bots:
Personen finden und Standort bestimmen
Kommunikation mit den Personen

Szenario: Waldbrand

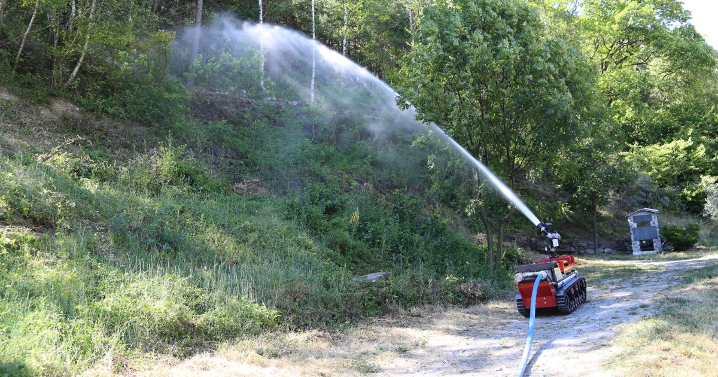
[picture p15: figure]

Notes: Benedikt

## Requirements

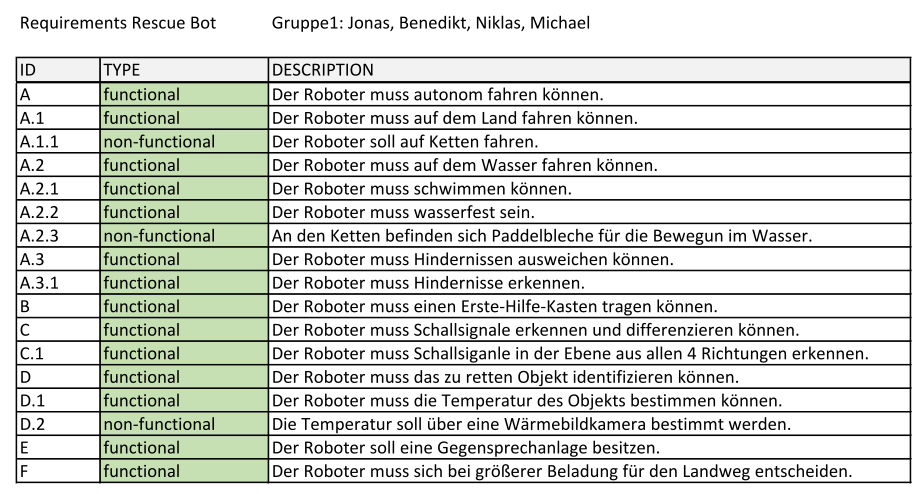
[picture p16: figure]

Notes: Benedikt

## Context modell

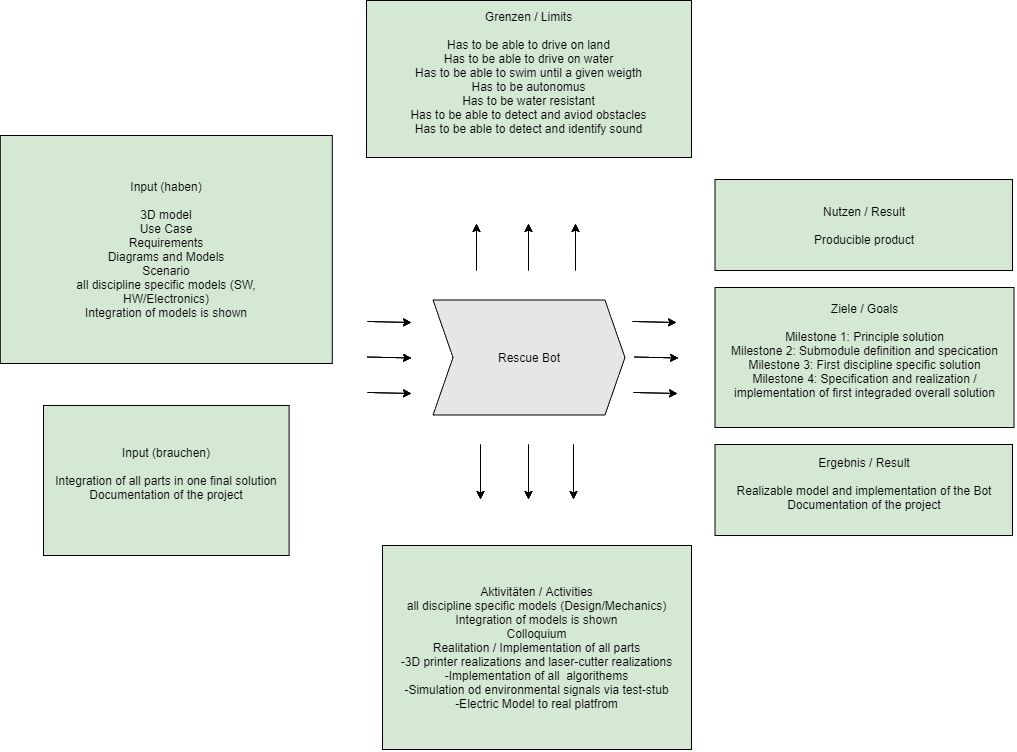
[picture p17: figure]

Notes: Niklas

## Use Case

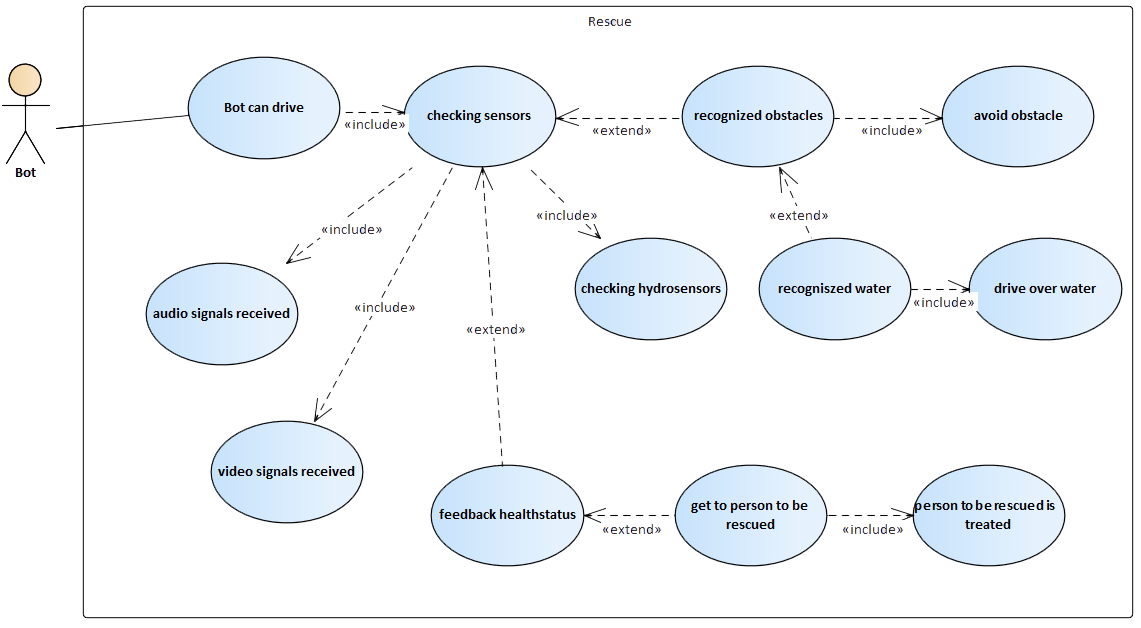
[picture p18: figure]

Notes: Jonas

## Stakeholder

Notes: Benedikt

## Stakeholder-Matrix

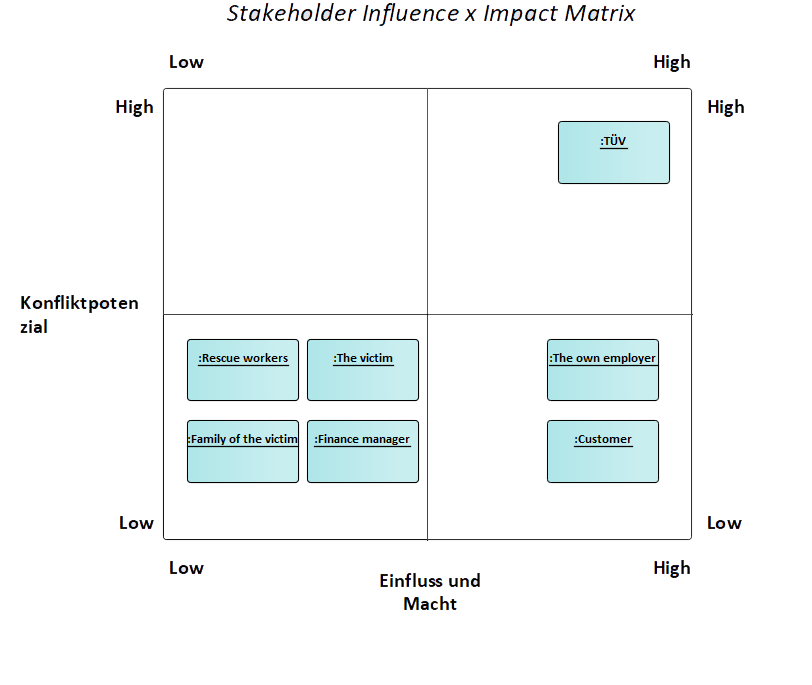
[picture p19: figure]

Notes: Benedikt

## Activity diagram

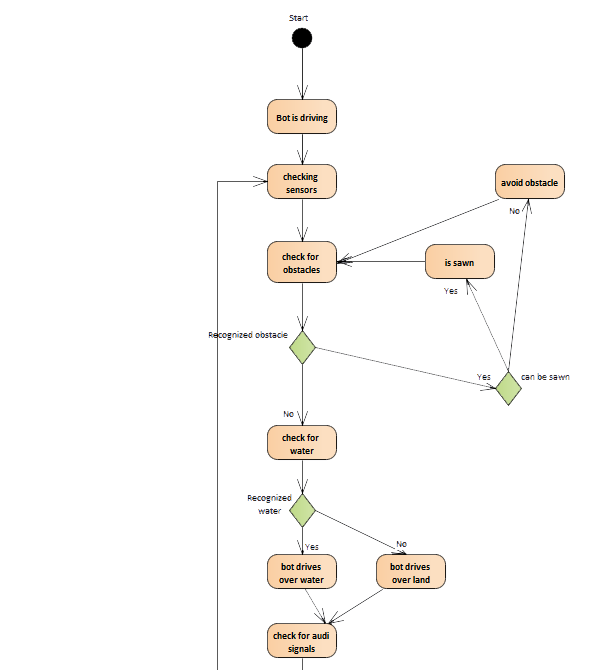
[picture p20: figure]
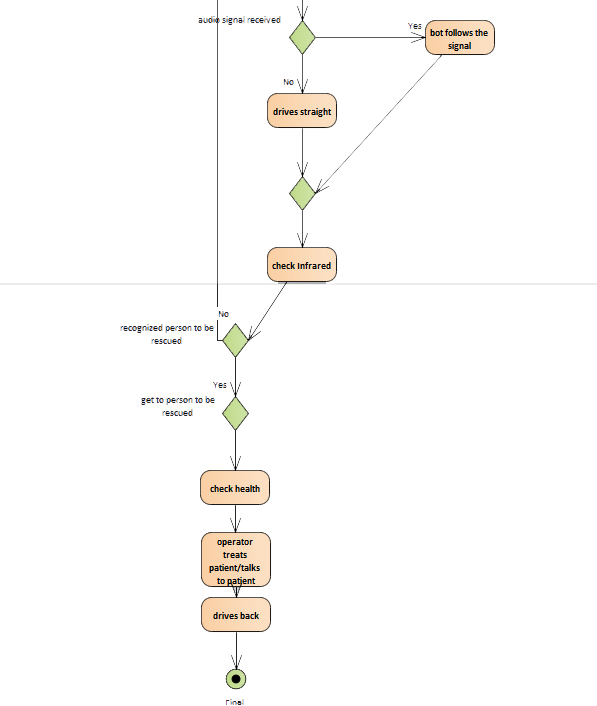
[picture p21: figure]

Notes: Jonas

## architecture diagram

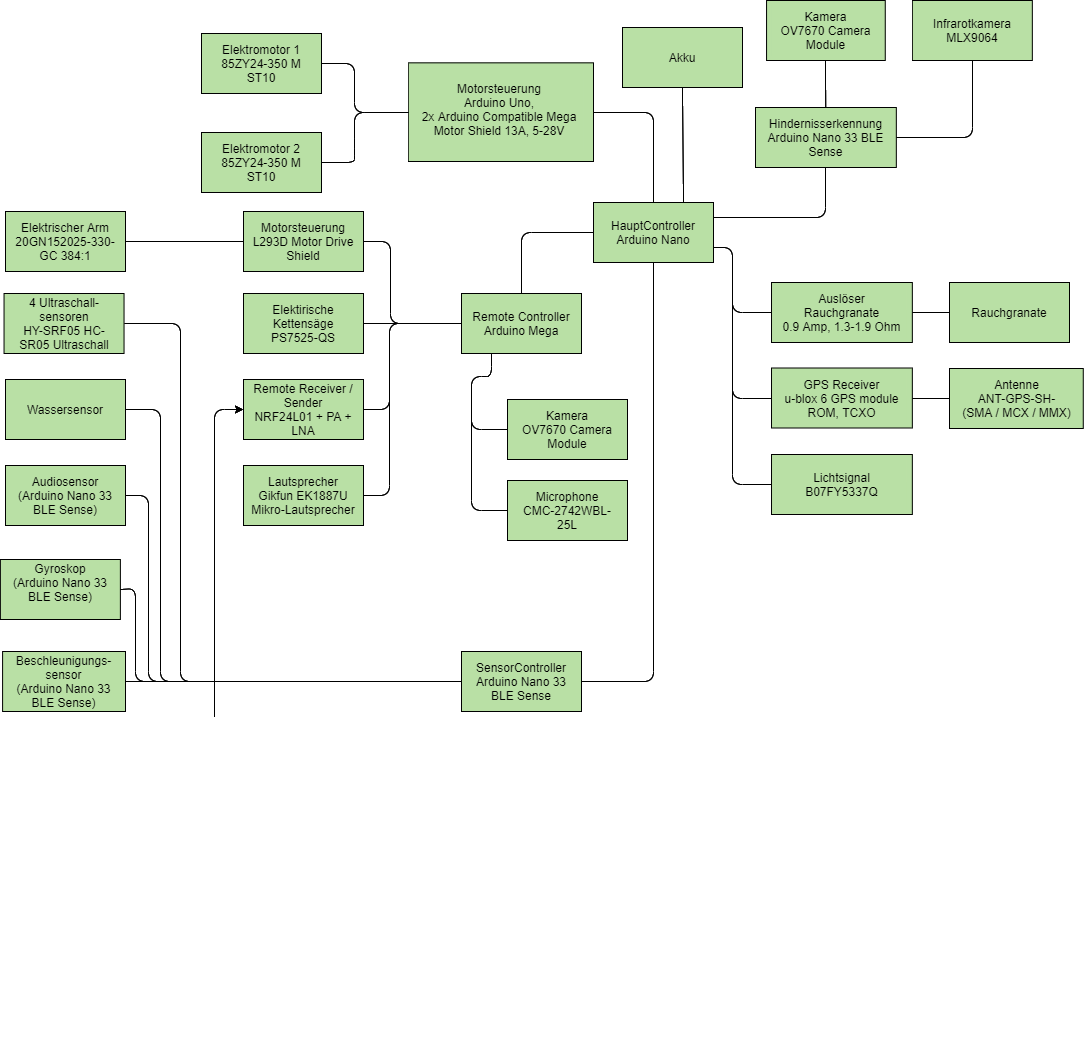
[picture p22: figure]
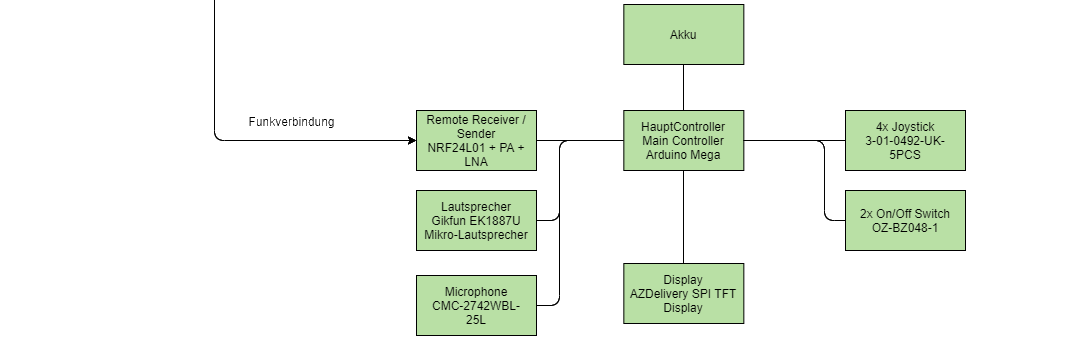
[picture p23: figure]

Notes: Niklas

## Schematic rescue bot

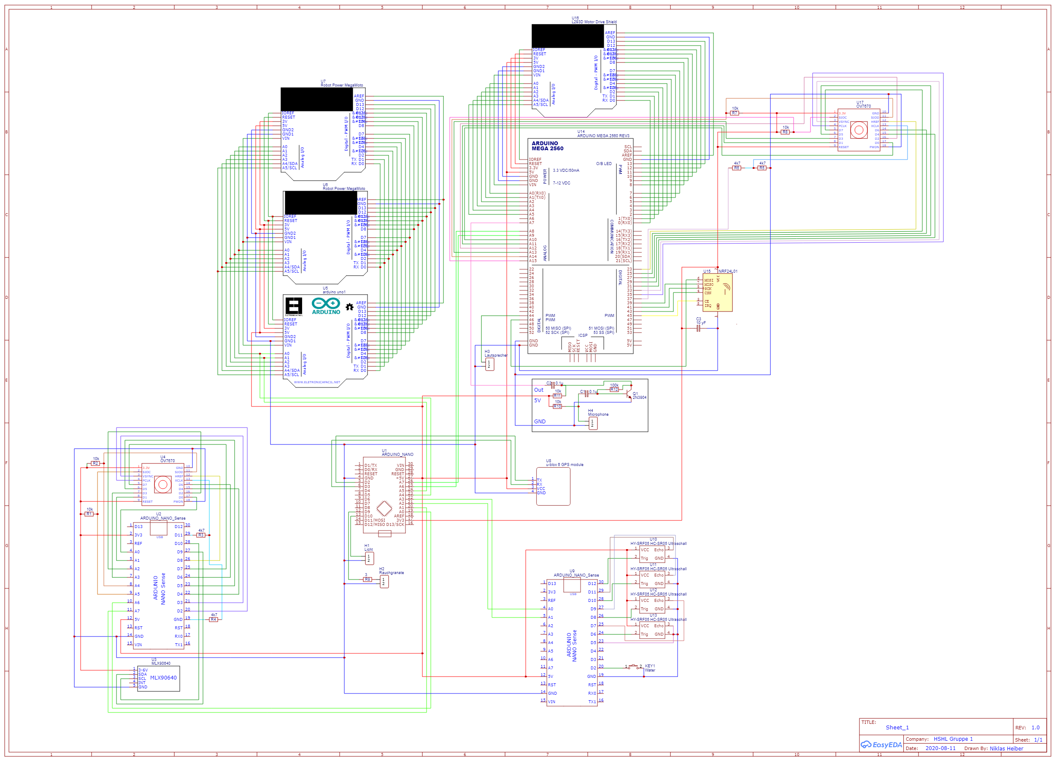
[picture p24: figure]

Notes: Niklas

## Schematic Remote Control

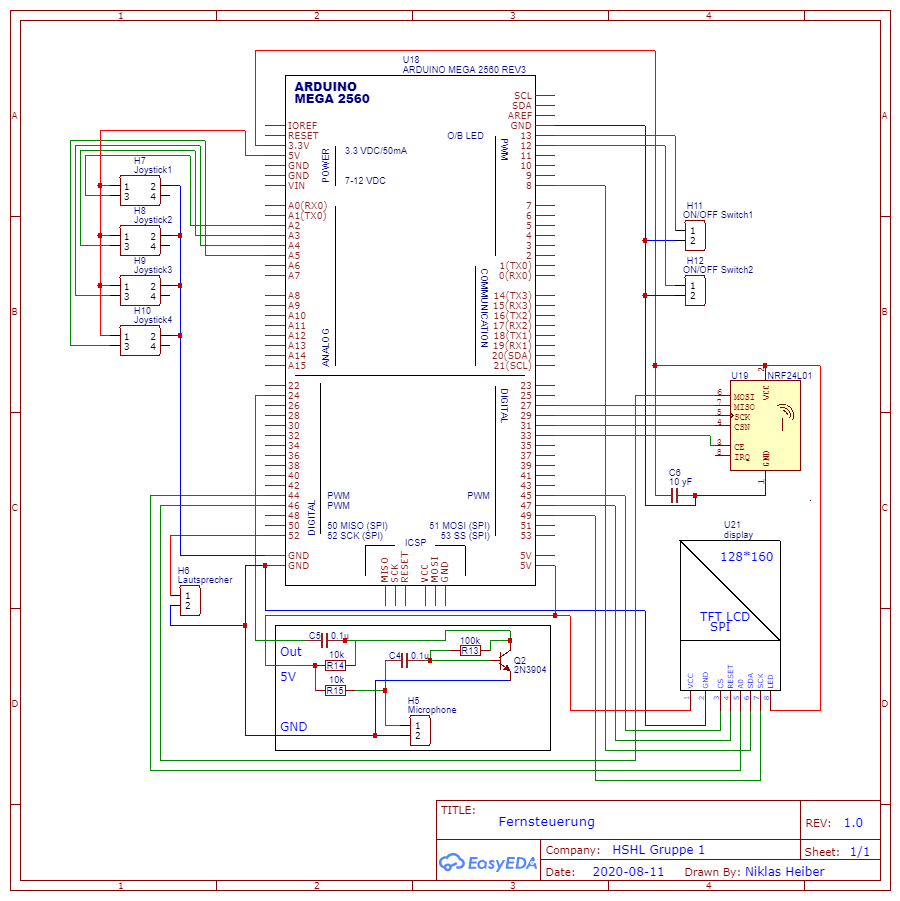
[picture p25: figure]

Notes: Niklas

## Class diagramm

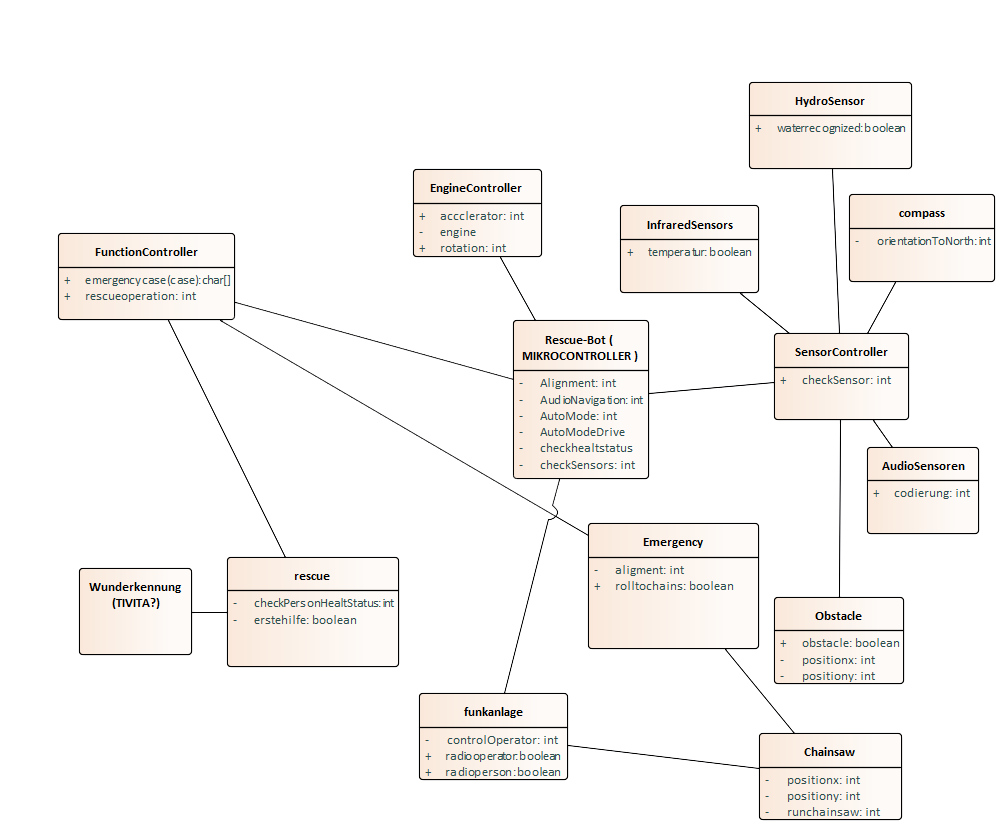
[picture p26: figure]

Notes: Benedikt

## State machine Audio Navigation


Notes: Benedikt

## Audio Navigation - Code


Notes: Benedikt

## State machine water


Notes: Niklas

## State machine object recognition


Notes: Jonas

## Paper Prototype

Erste Designidee
- Kettenantrieb
4 Schallsensoren
Kamera
Ablage für Erste-Hilfe-Set


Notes: Michael

## 3D-Modell

Gelenke mit Motoren


Kamera

Elektrokettensäge

Akku

Medikit

Drehteller

Omnidirektionales Mikrofon

Ultraschallsensoren

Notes: Michael

## 3D-Modell


- Abmessungen:
  - L: ca.750mm
  - B: 570mm
  - H: ca. 800mm

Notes: Michael

## 3D-Modell

Folgende Elemente werden noch hinzugefügt:
- Motoren
- Mikrocontroller
- Gegensprechanlage
- Rundumleuchte
- Elektr. zündbares Rauchsignal
- Antenne für Fernbedienung
- TIVITA System (http://diaspective-vision.com/produkte/ti-cam-system/)

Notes: Michael

## Umgebungsdiagramm


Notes: Michael

## Map- Übersicht


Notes: Michael

## Map Umsetzung


- Größe 30 X 30 Felder
- 4 Schallquellen in:
  - 3,3; 28,3 ; 27,26
R = Border
G = Ground
O = Obstacle
W =Water

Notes: Michael

## Die nächsten Schritte

- Projektkern
  - Bauteile für 3D-Drucker und Lasercutter auslegen
  - Algorithmen implementieren
  - Testumgebung simulieren
- Projektrahmen
  - Beginn Dokumentation
  - Diagramme überarbeiten

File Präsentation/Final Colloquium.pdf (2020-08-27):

Final Colloquium

Gruppe1

Niklas Heiber, Michael Jathe, Jonas Gerken, Benedikt Lipinski

Motivation

Szenario:Waldbrand


Einsatz des Bots:
- Personen finden und Standort bestimmen
- Kommunikation mit den
Personen

Requirements



Context model

Stakeholder


Stakeholder-Matrix

Use Case


Activity diagram

Swimlane


Swimlane

Top level architecture


Architecture model


Schematic rescue bot


Class diagramm


Mechanical copmosite structure diagram

State machine AutoModeDrive


State machine Ultrasonic

State machine Drive around right/left


State machine object recognition


State machine DriveMode

State machine audio navigation


Paper Prototype


- Erste Designidee
- Kettenantrieb
- 4 Schallsensoren
- Kamera
- Ablage für Erste-Hilfe-Set


3D-Model

Medikit

Ultraschall
sensoren

Omnidirektionales
Mikrofon

Akku
Elektrokettensäge

Kamera

Kettenantrieb
Rundumleuchte Funkantenne

Ein/Aus Schalter


3D-Model

24V DC-Motoren

24V Lipo

3D-Model

- Abmessungen:
– L: ca.750mm
– B: 570mm
– H: ca. 800mm


3D-Model


Teile sind druckbar !

3D-Model

- Schwimmkörpervolumen: ca. 7,9 Liter -> max. 7,9 kg Gesamgewicht
- Gewicht der Druckteile: ca. 5,7 kg
- Es bleiben 2,2kg für sämtliche Anbauteile (Säge, Elektronik, Akku, Ketten, Sensoren) -> Schwimmkörpervolumen sollte vergrößert werden


Test environment



Test environment

- Größe 30 X 30 Felder
- 4 Schallquellen in:
- 3,3; 3,28 ; 26,27

R = Border
G = Ground
O = Obstacle
W =Water

Fazit

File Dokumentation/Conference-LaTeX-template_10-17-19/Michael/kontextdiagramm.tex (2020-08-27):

\subsection{Kontextdiagramm}
-MJ-

Zu Beginn des Systementwurfs wurde ein Kontextdiagramm erstellt( siehe Abb. \ref{fig:context}). Das Kontextdiagramm dient zur Modellierung der Systemumgebung bildet die Schnittstellen zur Umwelt ab. So soll der Rettungsroboter z.B. eine Gegensprechanlage besitzen, um eine verbale Kommunikation zwischen dem Rettungsdienst und der zu rettenden Person zu ermöglichen. Außerdem wurden im Kontextdiagramm noch weitere Anforderungen spezifiziert. So soll die Hinderniserkennung mit Ultraschallsensoren umgesetzt werden.

\begin{figure}[h]
    \centering
    \captionsetup{width=.9\linewidth}
    
    \caption{Kontextdiagramm}
    \label{fig:context}
\end{figure}

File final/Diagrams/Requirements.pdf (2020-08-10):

Requirements Rescue Bot | Gruppe1: Jonas, Benedikt, Niklas, Michael
ID | TYPE | DESCRIPTION
A | functional | Der Roboter muss autonom fahren können.
A.1 | functional | Der Roboter muss auf dem Land fahren können.
A.1.1 | non-functional | Der Roboter soll auf Ketten fahren.
A.2 | functional | Der Roboter muss auf dem Wasser fahren können.
A.2.1 | functional | Der Roboter muss schwimmen können.
A.2.2 | functional | Der Roboter muss wasserfest sein.
A.2.3 | non-functional | An den Ketten befinden sich Paddelbleche für die Bewegun im Wasser.
A.3 | functional | Der Roboter muss Hindernissen ausweichen können.
A.3.1 | functional | Der Roboter muss Hindernisse erkennen.
B | functional | Der Roboter muss einen Erste-Hilfe-Kasten tragen können.
C | functional | Der Roboter muss Schallsignale erkennen und differenzieren können.
C.1 | functional | Der Roboter muss Schallsiganle in der Ebene aus allen 4 Richtungen erkennen.
D | functional | Der Roboter muss das zu retten Objekt identifizieren können.
D.1 | functional | Der Roboter muss die Temperatur des Objekts bestimmen können.
D.2 | non-functional | Die Temperatur soll über eine Wärmebildkamera bestimmt werden.
E | functional | Der Roboter soll eine Gegensprechanlage besitzen.
F | functional | Der Roboter muss sich bei größerer Beladung für den Landweg entscheiden.

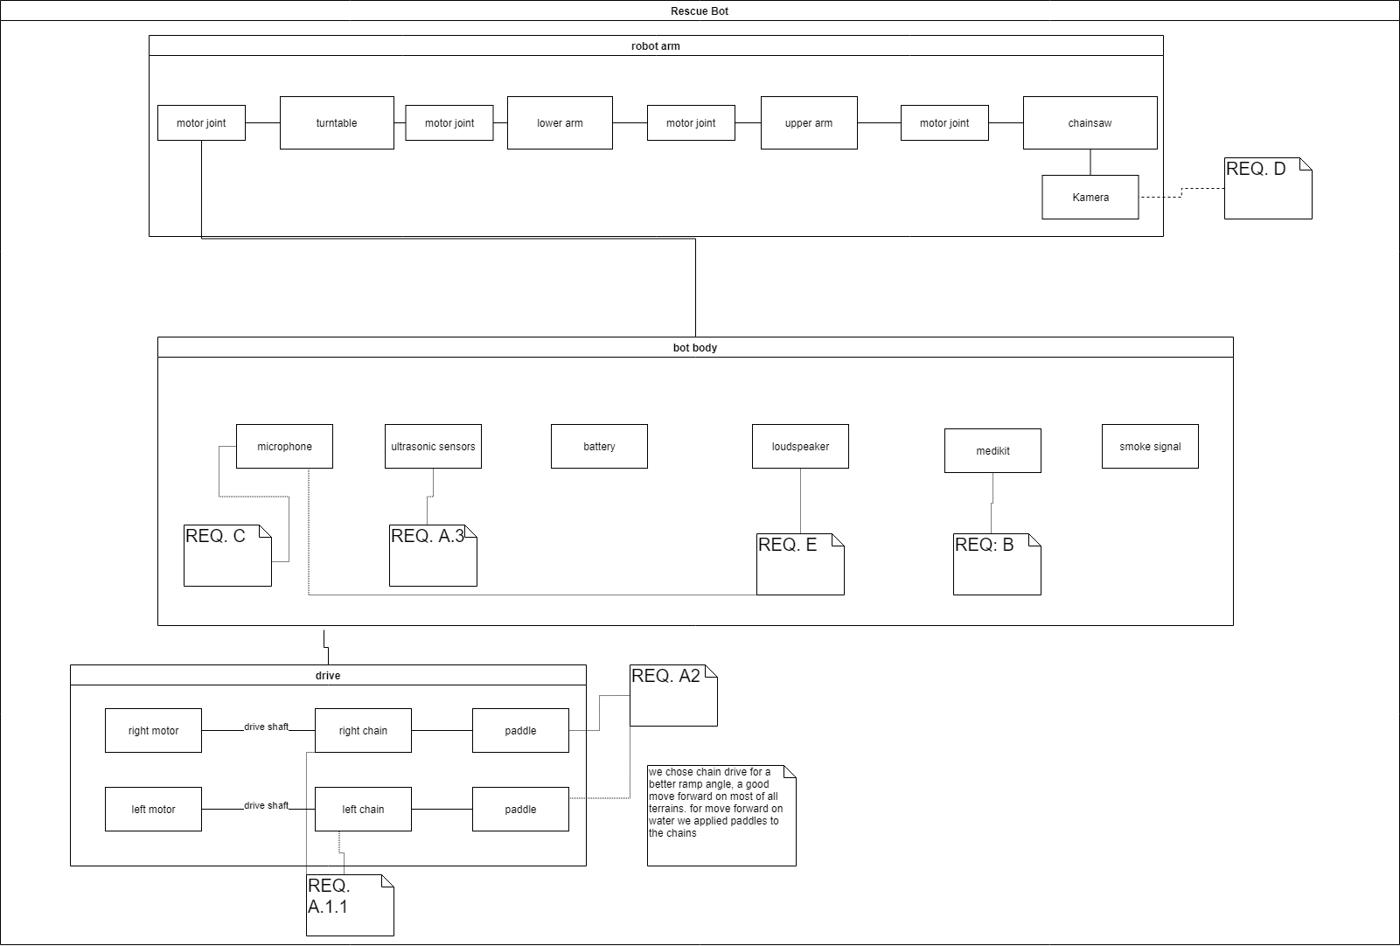
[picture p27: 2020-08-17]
final/Diagrams/mechanical_copmosite_structure_diagram.png

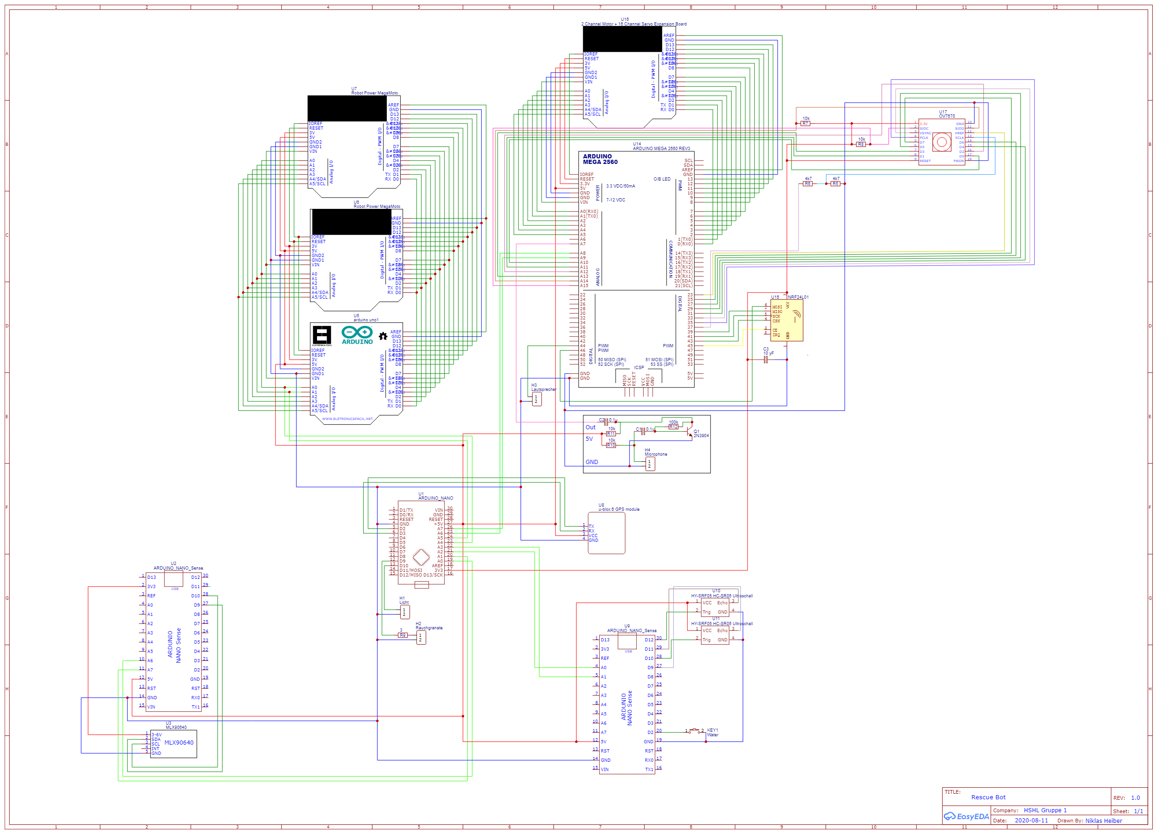
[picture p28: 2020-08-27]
final/Diagrams/Schematic_Rescue-Bot.png

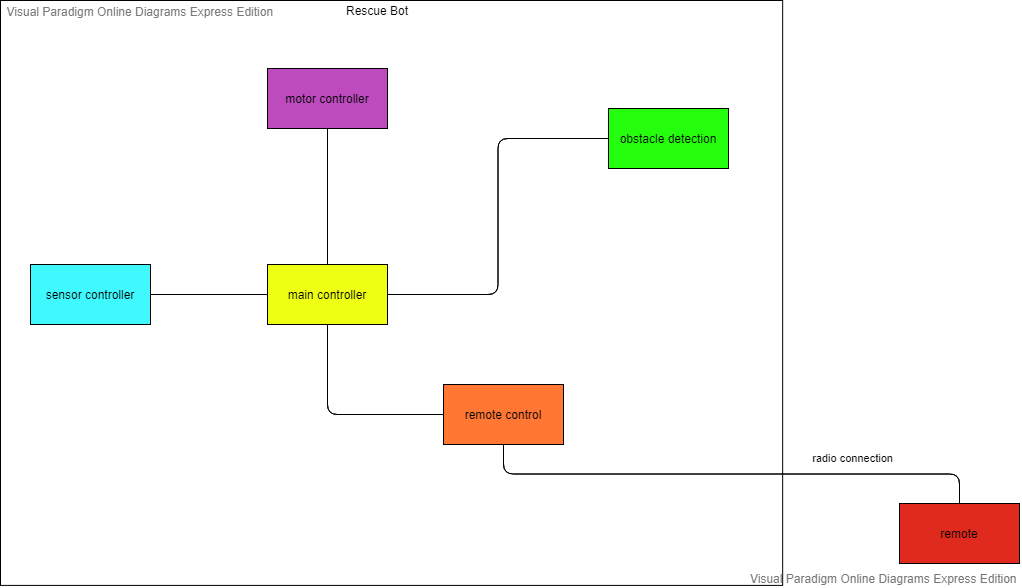
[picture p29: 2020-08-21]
final/Diagrams/top_level_architecture.png

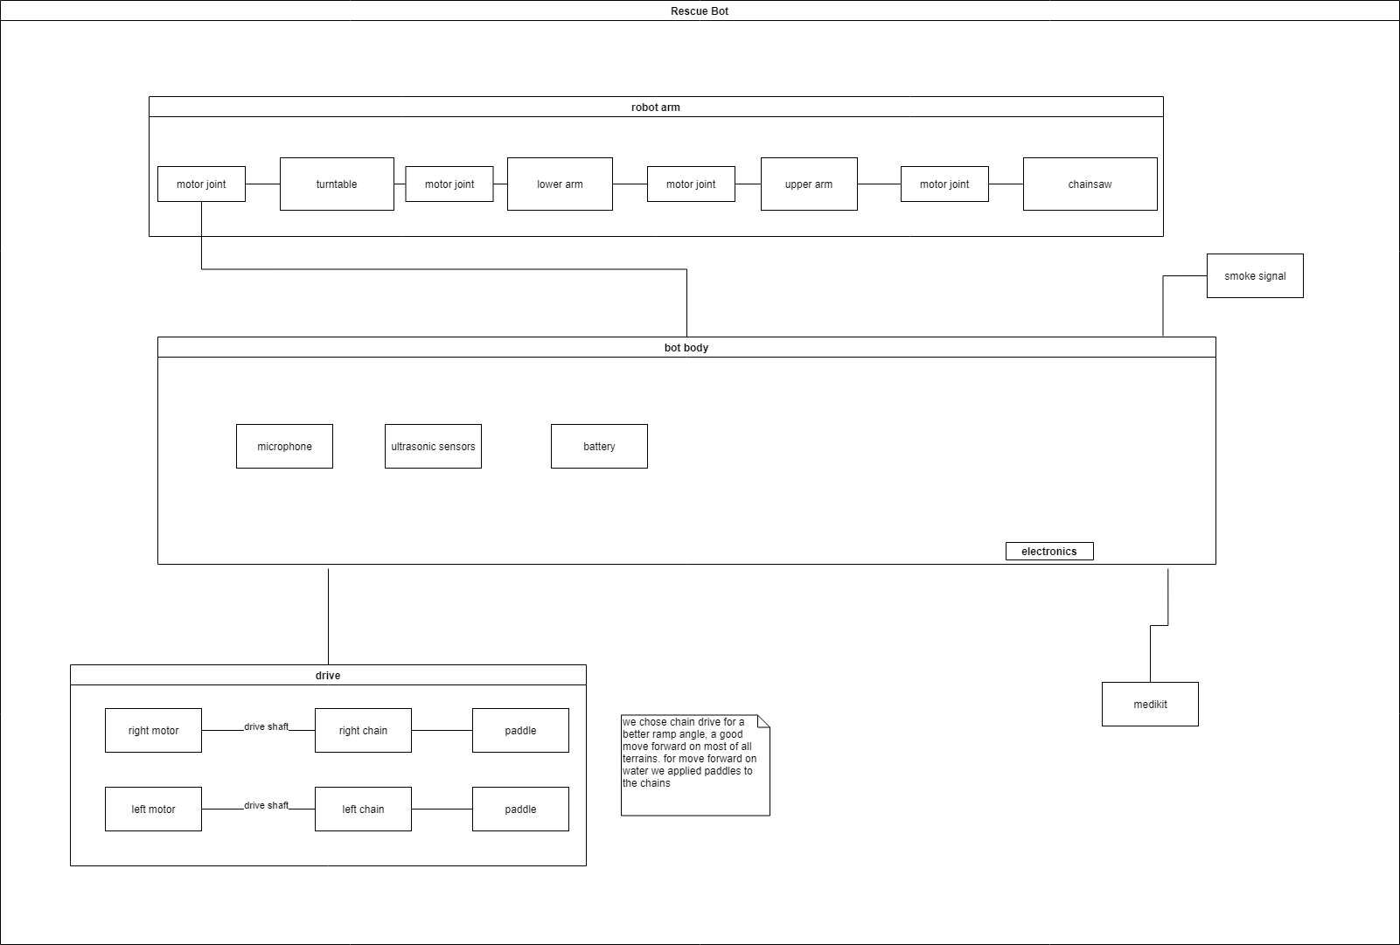
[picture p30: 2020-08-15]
REVISION/diagrams/in_progress/mechanical_copmosite_structure_diagram.png

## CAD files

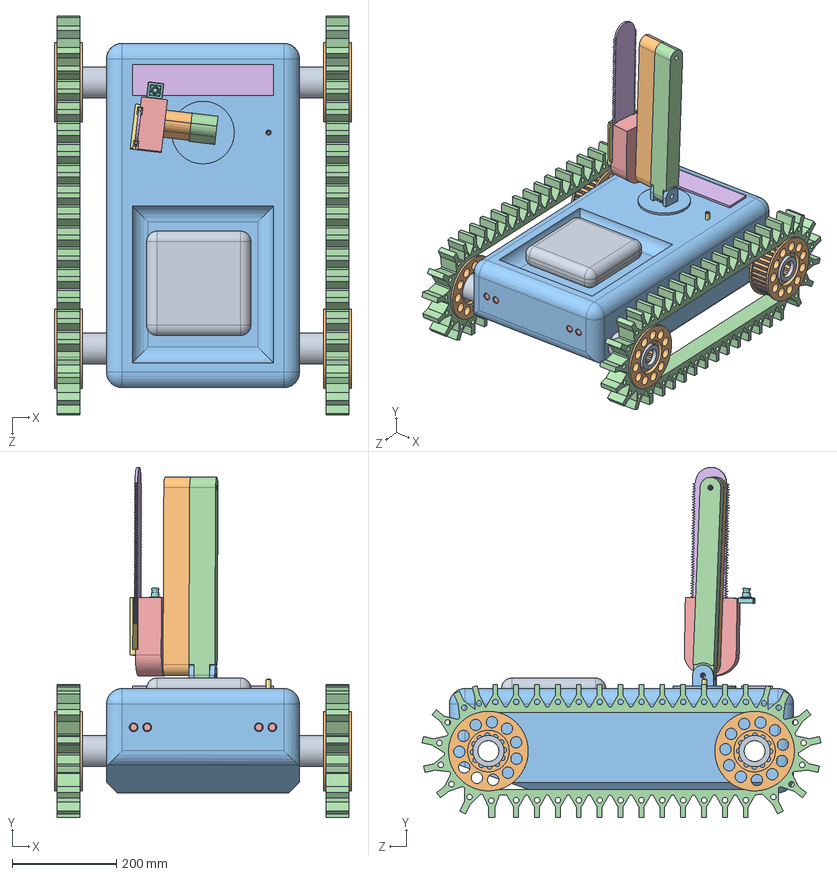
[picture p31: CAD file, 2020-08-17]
3D-Modell/rescue_bot_prototype3.SLDASM
570.0 x 671.3 x 764.5 mm
between x 4
wheel (pulley) x 4
belt2 x 2
Ultraschallsensor x 4
Akku
microphone_adapter
microphone
medikit
arm_oben
drehscheibe
Arm_unten
säge_gehäuse
kette
säge_deckel
camera

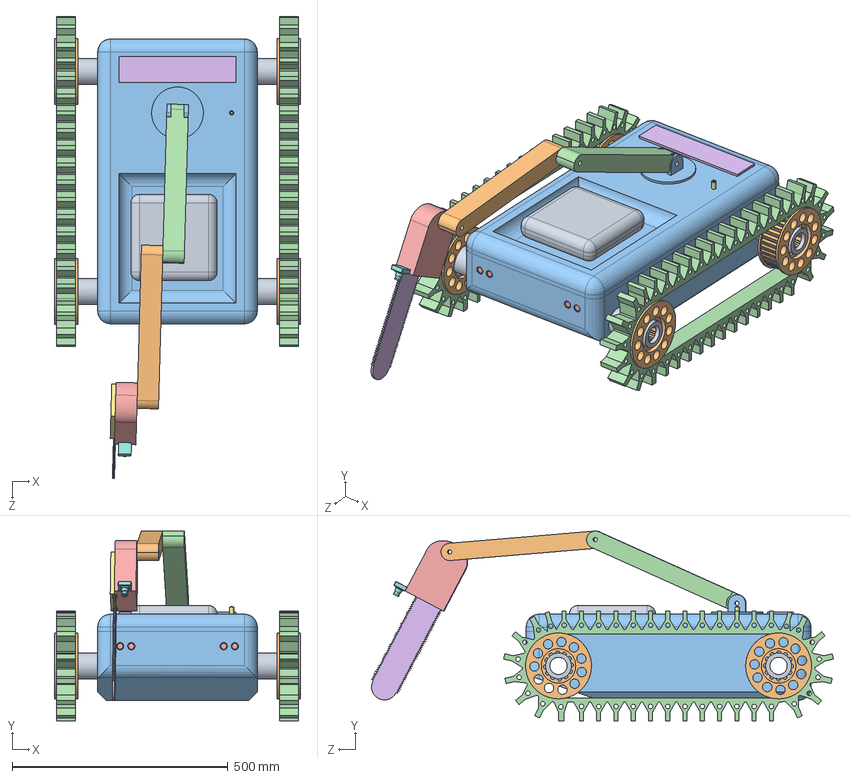
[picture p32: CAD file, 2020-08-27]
PaperPrototyping/3D-Modell/rescue_bot_prototype3.SLDASM
570.0 x 440.1 x 1070.6 mm
between x 4
wheel (pulley) x 4
belt2 x 2
Ultraschallsensor x 4
Akku
microphone_adapter
microphone
medikit
arm_oben
drehscheibe
Arm_unten
säge_gehäuse
kette
säge_deckel
camera

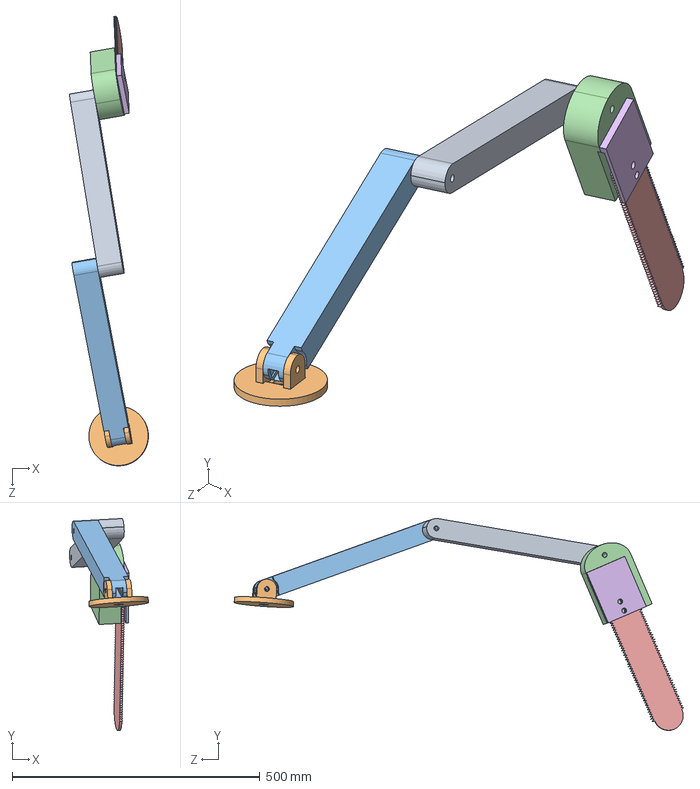
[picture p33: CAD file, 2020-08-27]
final/3D-Modell/roboterarm_revision/robot_arm.SLDASM
159.3 x 427.7 x 907.3 mm
arm_oben
drehscheibe
Arm_unten
säge_gehäuse
kette
säge_deckel

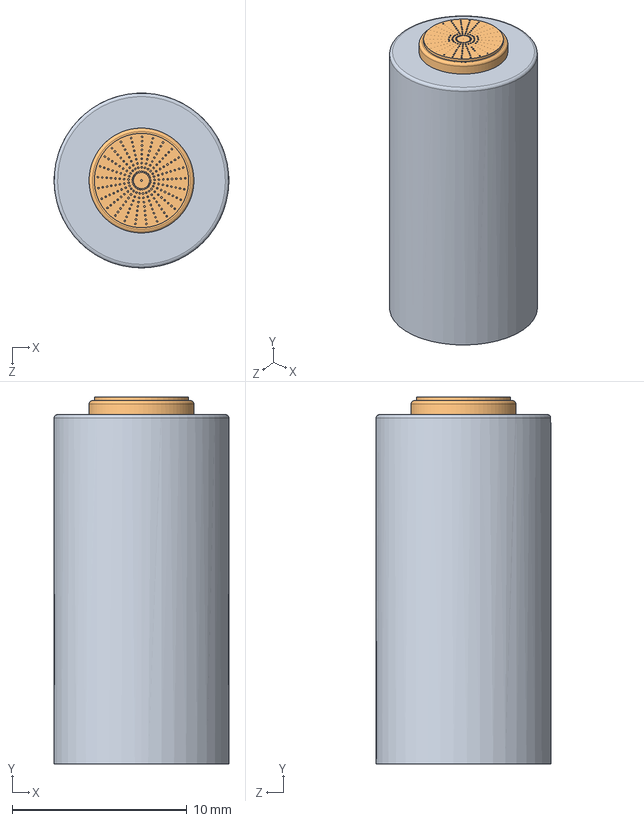
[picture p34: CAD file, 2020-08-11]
PaperPrototyping/3D-Modell/microphone_group.SLDASM
10.00 x 21.0 x 10.0 mm
microphone_adapter
microphone

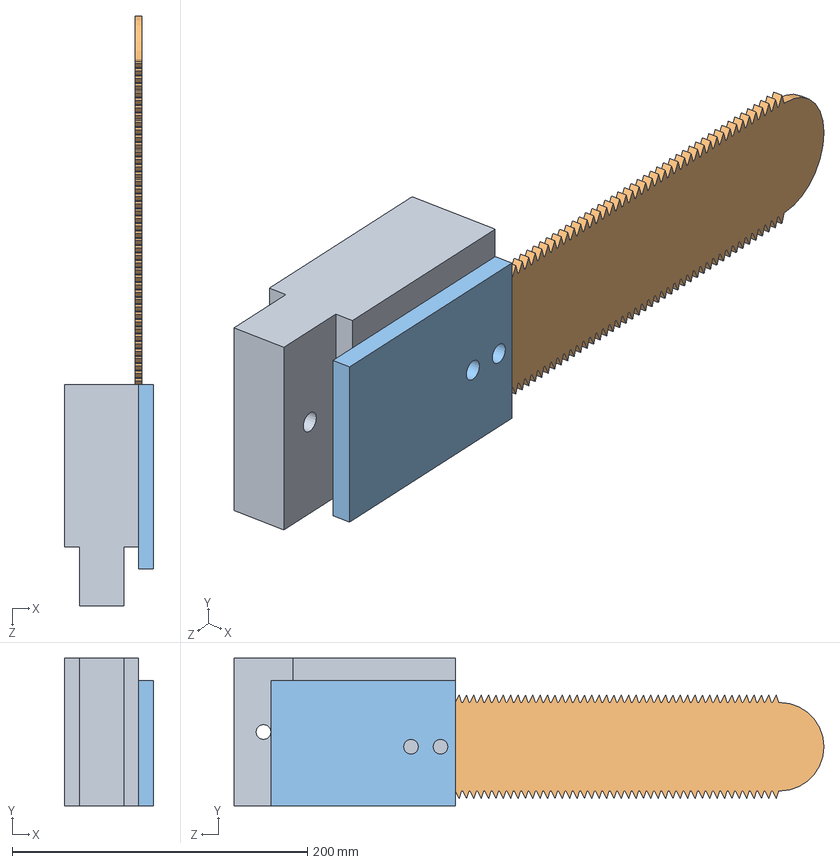
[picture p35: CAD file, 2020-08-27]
final/3D-Modell/baugruppe_säge.SLDASM
60.0 x 100.0 x 400.0 mm
säge_gehäuse
kette
säge_deckel

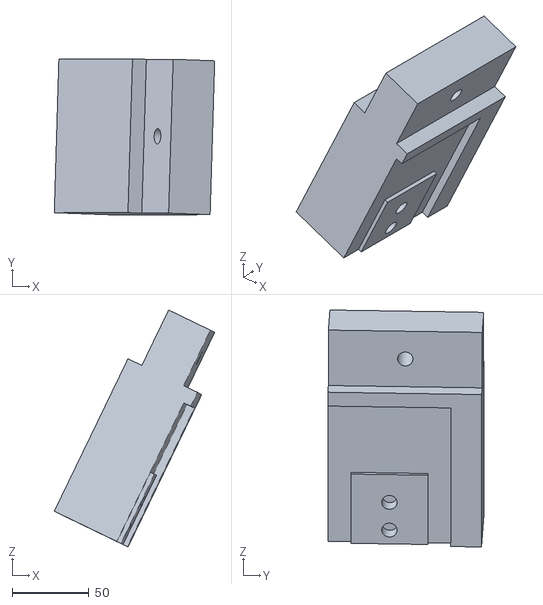
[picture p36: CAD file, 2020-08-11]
final/3D-Modell/stl/rescue_bot_prototype2 - Roboter_arm_v1-1 baugruppe_säge-1 säge_gehäuse-1.STL
104.2 x 101.6 x 154.0

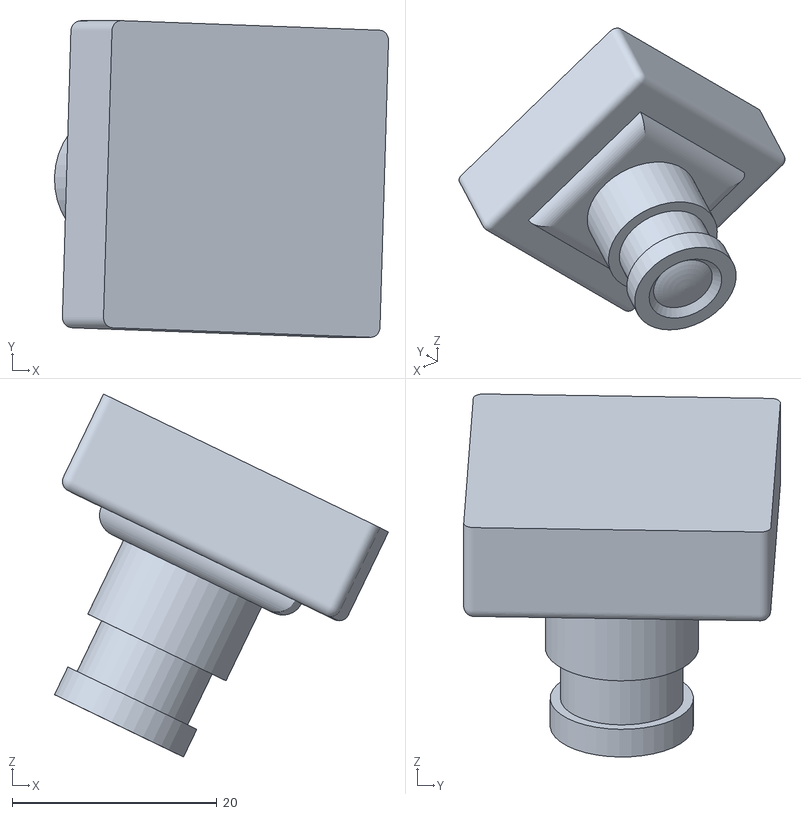
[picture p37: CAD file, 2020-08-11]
final/3D-Modell/stl/rescue_bot_prototype2 - Roboter_arm_v1-1 baugruppe_säge-1 camera-1.STL
32.6 x 30.9 x 35.4

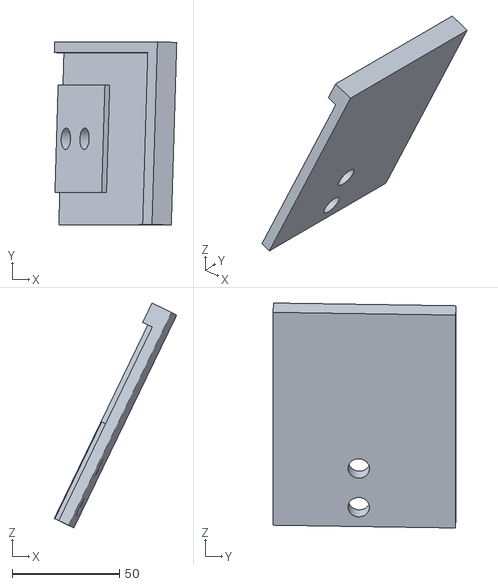
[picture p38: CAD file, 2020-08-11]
final/3D-Modell/stl/rescue_bot_prototype2 - Roboter_arm_v1-1 baugruppe_säge-1 säge_deckel-1.STL
57.0 x 85.4 x 104.7

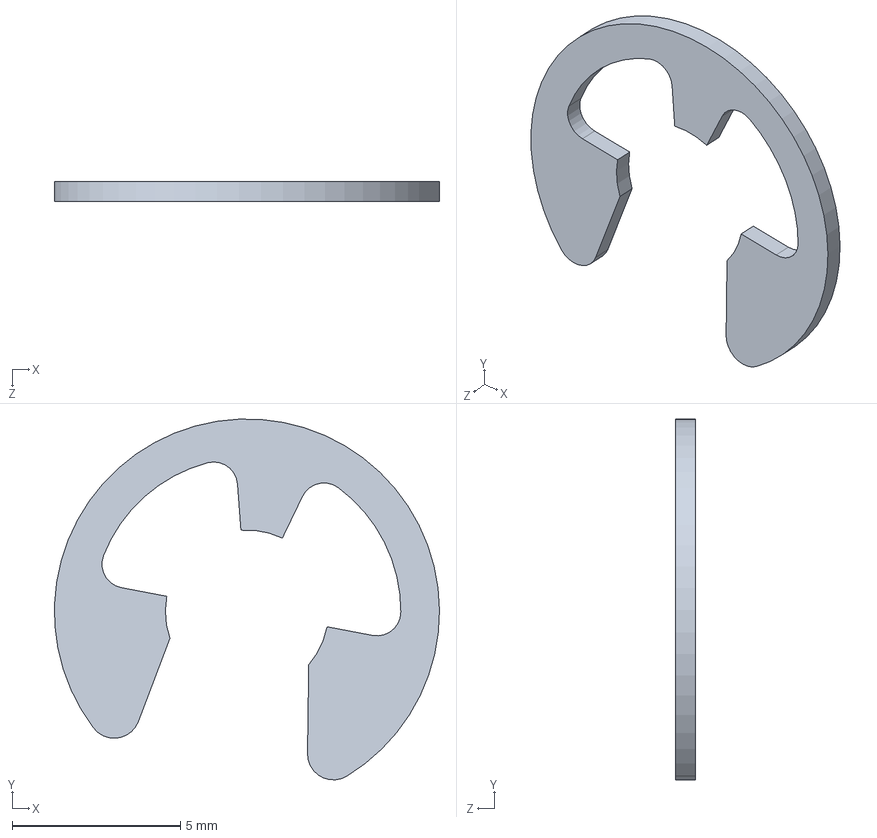
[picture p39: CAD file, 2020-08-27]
final/3D-Modell/final/Faulhaber_2342L012CRfinal.SLDASM
11.4 x 10.7 x 0.6 mm

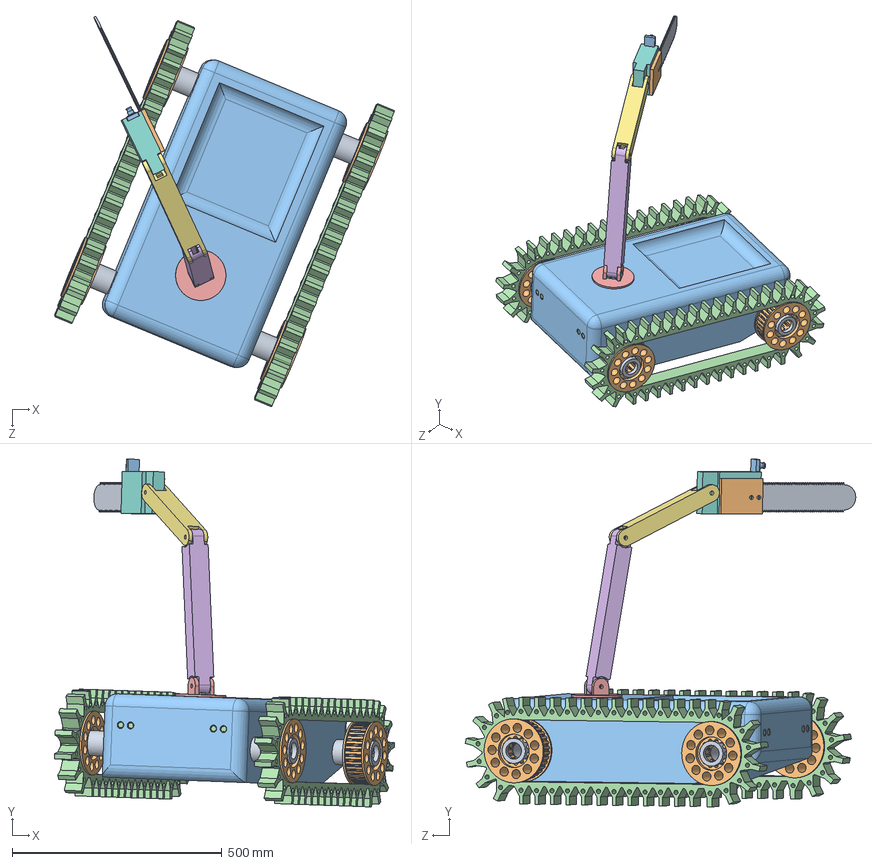
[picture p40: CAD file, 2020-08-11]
final/3D-Modell/rescue_bot_prototype2.SLDASM
810.5 x 829.4 x 931.2 mm
between x 4
wheel (pulley) x 4
belt2 x 2
drehscheibe
Arm_unten
arm_oben
säge_gehäuse
kette
säge_deckel
camera
Ultraschallsensor x 4

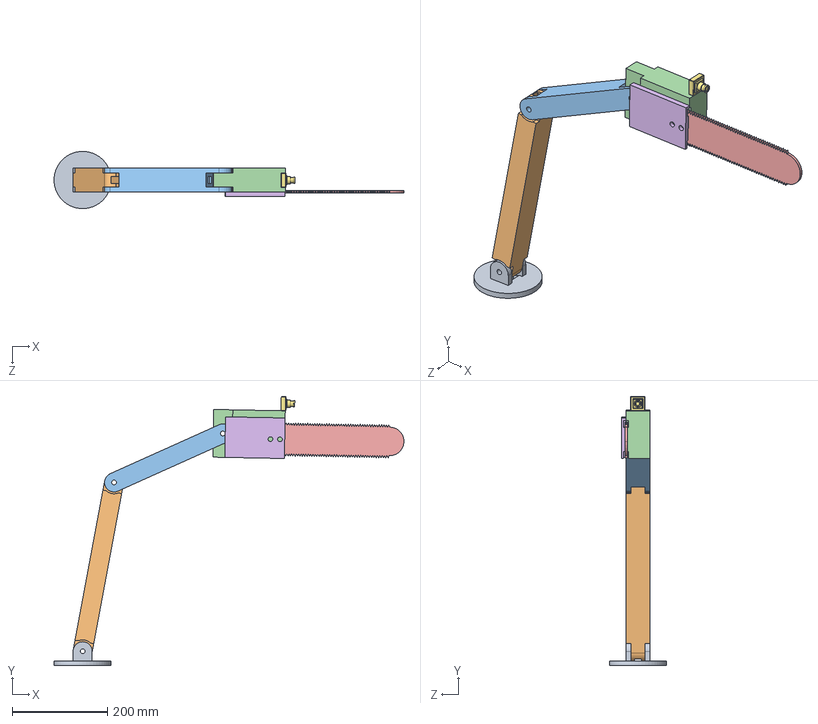
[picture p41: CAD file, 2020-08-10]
final/3D-Modell/Roboter_arm_v1.SLDASM
733.6 x 564.1 x 120.0 mm
drehscheibe
Arm_unten
arm_oben
säge_gehäuse
kette
säge_deckel
camera

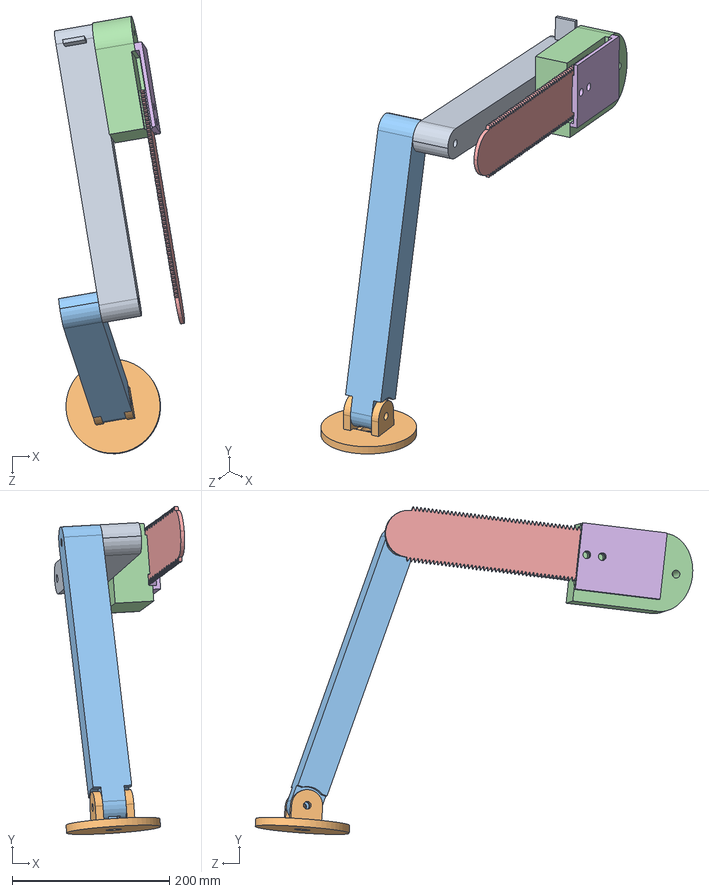
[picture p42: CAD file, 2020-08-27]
final/3D-Modell/final/robot_armfinal.SLDASM
165.8 x 417.3 x 556.7 mm
arm_obenfinal
drehscheibefinal
Arm_untenfinal
säge_gehäusefinal
kettefinal
säge_deckelfinal

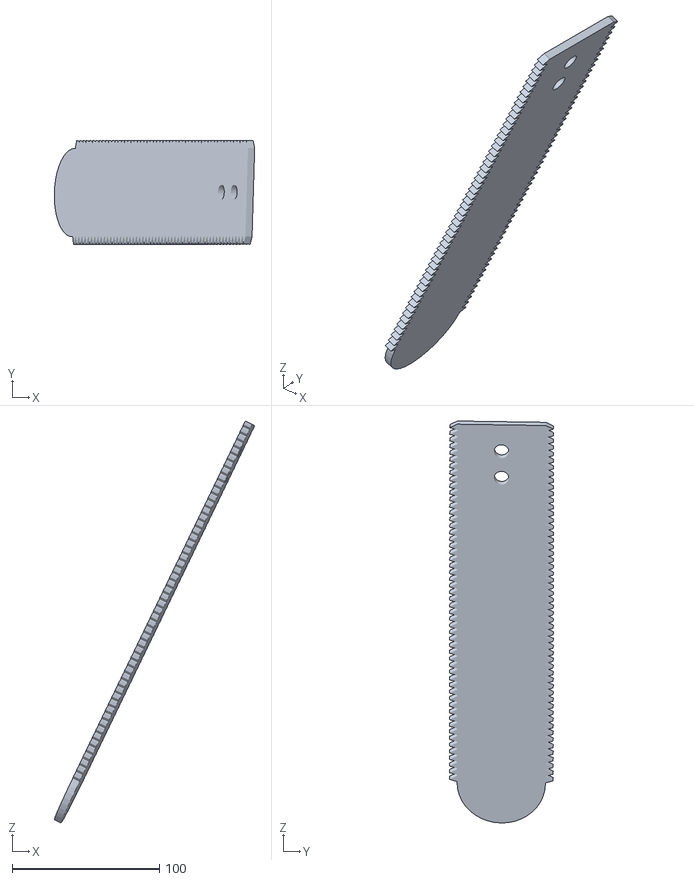
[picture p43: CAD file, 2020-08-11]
final/3D-Modell/stl/rescue_bot_prototype2 - Roboter_arm_v1-1 baugruppe_säge-1 kette-1.STL
135.9 x 70.7 x 272.7

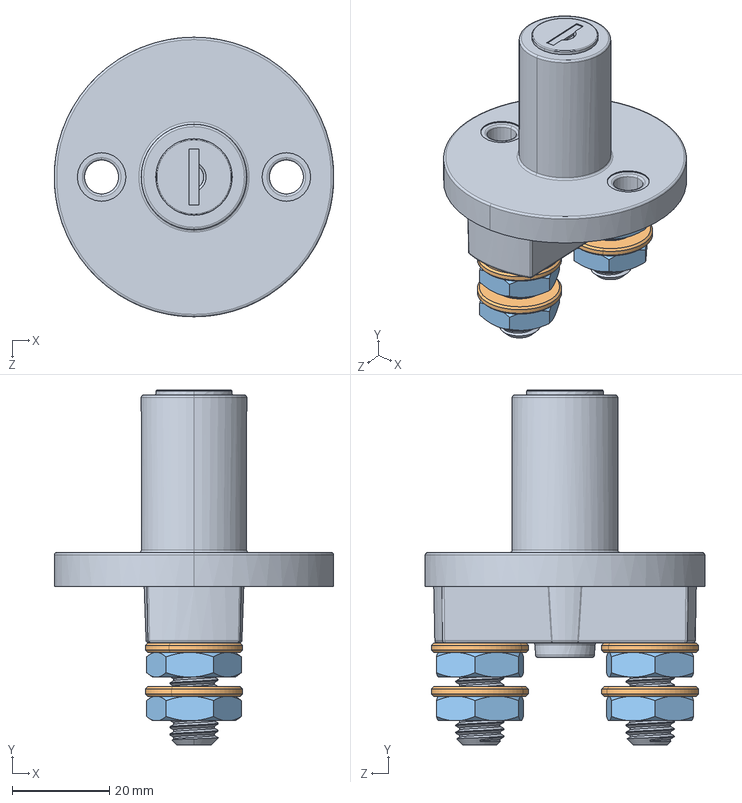
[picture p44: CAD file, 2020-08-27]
final/3D-Modell/final/zündschlüsselfinal.SLDASM
57.4 x 73.0 x 57.5 mm
0-605-21.STEP
0-605-21-01.STEP x 4
0-605-21-02.STEP x 4

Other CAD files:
final/3D-Modell/final/AssemMotorfinal.SLDASM
final/3D-Modell/final/microphone_groupfinal.SLDASM
final/3D-Modell/final/baugruppe_sägefinal.SLDASM
final/3D-Modell/final/AssemGearfinal.SLDASM
3D-Modell/roboterarm_revision/arm_oben.SLDPRT
PaperPrototyping/3D-Modell/rescue_bot_technische_zeichung.SLDDRW
final/3D-Modell/Arm_unten.SLDPRT
final/3D-Modell/Baugruppe.SLDASM
final/3D-Modell/Ultraschallsensor.SLDPRT
final/3D-Modell/arm_oben.SLDPRT
final/3D-Modell/belt.SLDPRT
final/3D-Modell/belt2.SLDPRT
final/3D-Modell/between.SLDPRT
final/3D-Modell/body.SLDPRT
final/3D-Modell/camera.SLDPRT
final/3D-Modell/deckel.sldprt
final/3D-Modell/drehscheibe.SLDPRT
final/3D-Modell/final/0-605-21.STEP
final/3D-Modell/final/Akkufinal.SLDPRT
final/3D-Modell/final/Antennafinal.SLDPRT
final/3D-Modell/final/Arm_untenfinal.SLDPRT
final/3D-Modell/final/Baquela_Encoderfinal.SLDPRT
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

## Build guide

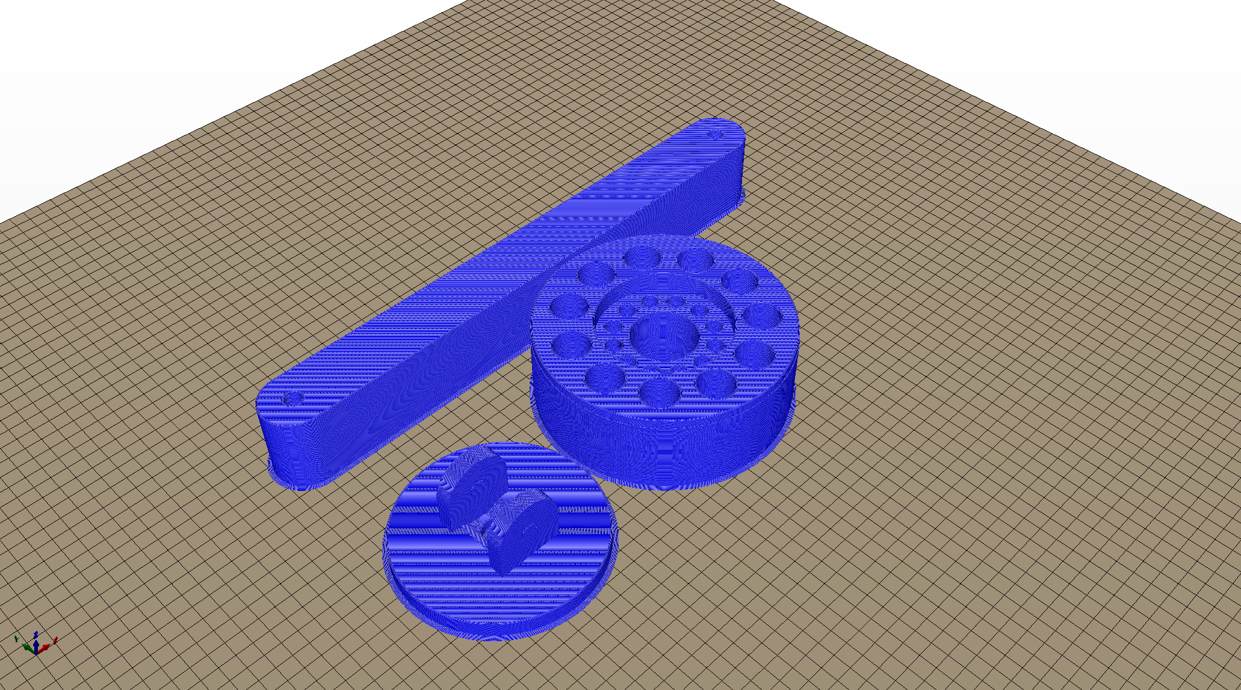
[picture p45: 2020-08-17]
final/3D-Modell/printable/wheel+drehscheibe+arm.png

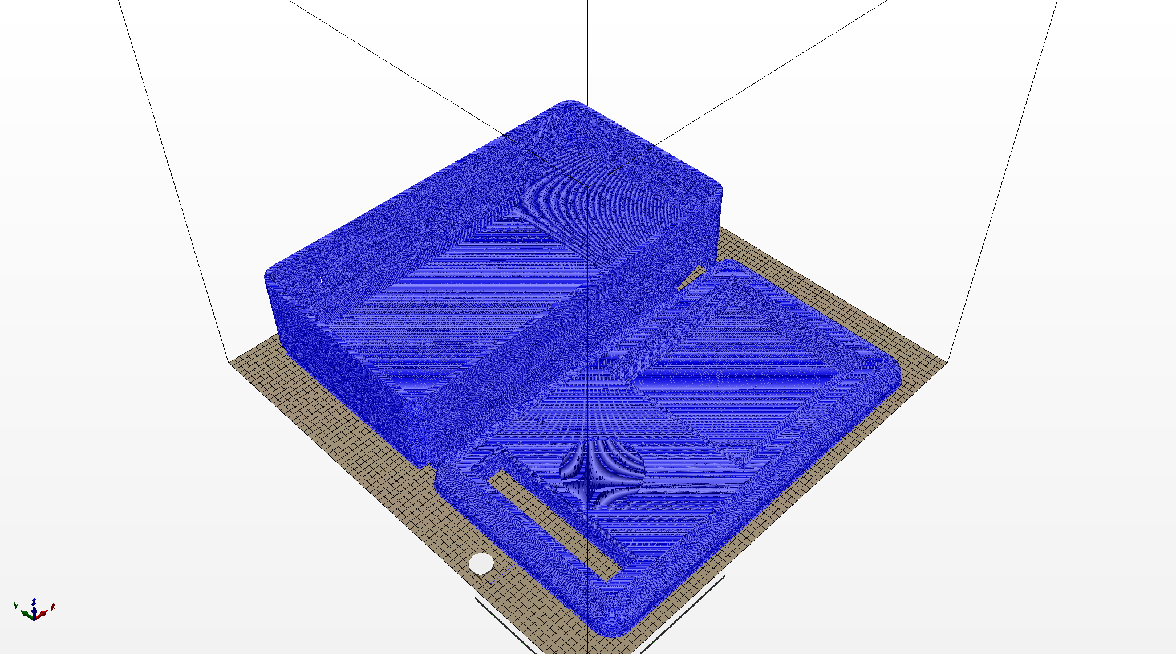
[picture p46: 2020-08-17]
final/3D-Modell/printable/wanne+deckel.png

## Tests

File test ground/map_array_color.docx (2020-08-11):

{{"R","R","R","R","R","R","R","R","R","R","R","R","R","R","R","R","R","R","R","R","R","R","R","R","R","R","R","R","R","R"},

{"R","G","G","G","R","R","R","R","R","G","G","G","G","R","R","R","G","G","G","G","G","G","G","G","G","G","G","G","G","R"},

{"R","G","G","G","G","G","G","G","G","G","G","G","G","G","G","G","G","G","G","G","G","G","G","G","G","G","G","G","G","R"},

{"R","G","G","G","G","G","G","G","G","G","G","G","G","G","G","G","G","G","G","G","G","G","G","G","G","G","G","O","G","R"},

{"R","G","O","O","G","G","G","G","G","G","G","G","G","G","G","G","G","G","G","G","G","O","O","G","G","G","G","O","G","R"},

{"R","G","O","O","G","G","G","G","O","O","O","G","G","O","O","O","O","O","O","O","O","O","O","G","G","G","G","G","G","R"},

{"R","G","G","G","G","G","G","G","O","O","O","G","G","O","O","O","O","O","O","O","O","O","O","G","G","G","O","G","G","R"},

{"R","G","G","G","G","G","G","G","O","O","O","O","O","O","O","O","O","O","O","O","O","O","O","O","O","O","O","G","G","R"},

{"R","G","G","G","G","G","G","G","O","O","O","O","O","O","O","O","O","O","O","O","O","O","O","O","O","O","O","G","G","R"},

{"R","G","G","G","G","G","G","G","O","O","O","O","O","O","O","O","O","O","O","O","O","O","O","O","O","O","G","G","G","R"},

{"R","G","G","G","G","G","G","G","O","O","O","O","O","O","O","O","O","O","O","O","O","O","O","O","O","O","G","G","G","R"},

{"R","G","G","G","G","G","G","G","O","O","O","O","O","O","O","O","O","O","O","O","O","O","O","O","O","G","G","G","G","R"},

{"R","G","G","G","G","G","G","G","G","O","O","O","O","O","O","O","O","O","O","O","O","O","O","O","O","G","G","G","G","R"},

{"R","G","G","G","G","G","G","G","G","O","O","O","O","O","O","O","O","O","O","O","O","O","O","O","O","G","G","G","G","R"},

{"R","G","G","G","G","G","G","G","G","O","O","O","O","O","O","O","O","O","O","O","O","O","O","O","O","G","G","G","R","R"},

{"R","G","G","G","G","G","G","G","G","O","O","O","O","O","O","O","O","O","O","O","O","O","O","O","O","G","G","G","R","R"},

{"R","G","G","G","G","G","G","G","G","O","O","O","O","O","O","O","O","O","O","O","O","O","O","O","O","G","G","G","R","R"},

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

{"R","R","R","G","G","G","G","G","G","O","O","O","O","O","O","O","O","O","O","O","O","O","O","O","O","G","G","G","G","R"},

{"R","R","R","G","G","G","G","G","G","G","G","G","G","W","W","W","W","W","W","W","G","G","G","G","G","G","G","G","G","R"},

{"R","R","R","G","G","G","G","G","G","G","G","G","G","W","W","W","W","W","W","W","G","G","G","G","G","G","G","G","G","R"},

{"R","G","G","G","G","G","G","G","G","G","G","G","W","W","W","W","W","W","W","W","W","G","G","G","G","G","G","G","G","R"},

{"R","G","G","G","G","G","G","G","G","G","G","G","W","W","O","W","W","W","W","W","W","G","G","G","G","G","G","G","G","R"},

{"R","G","G","G","G","G","G","G","G","G","G","W","W","W","W","W","W","W","W","W","W","W","G","G","G","G","G","G","G","R"},

{"R","G","G","G","G","R","R","R","R","R","R","W","W","W","W","W","W","W","W","W","W","W","G","G","R","G","G","G","G","R"},

{"R","G","G","G","G","R","R","R","R","R","R","W","W","W","W","W","W","W","W","W","W","W","R","R","R","R","G","G","R","R"},

{"R","G","G","G","G","R","R","R","R","R","R","G","W","W","O","W","W","W","W","W","W","R","R","R","R","R","R","G","R","R"},

{"R","R","R","R","R","R","R","R","R","R","R","R","R","R","R","R","R","R","R","R","R","R","R","R","R","R","R","R","R","R"},

}

R = Border

G = Ground

O = Obstacle

W = Water

Schallquellen in 3,3 28,3 und 28,28

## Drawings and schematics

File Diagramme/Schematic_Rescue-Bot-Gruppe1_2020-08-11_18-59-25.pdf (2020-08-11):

## ARDUINO MEGA 2560

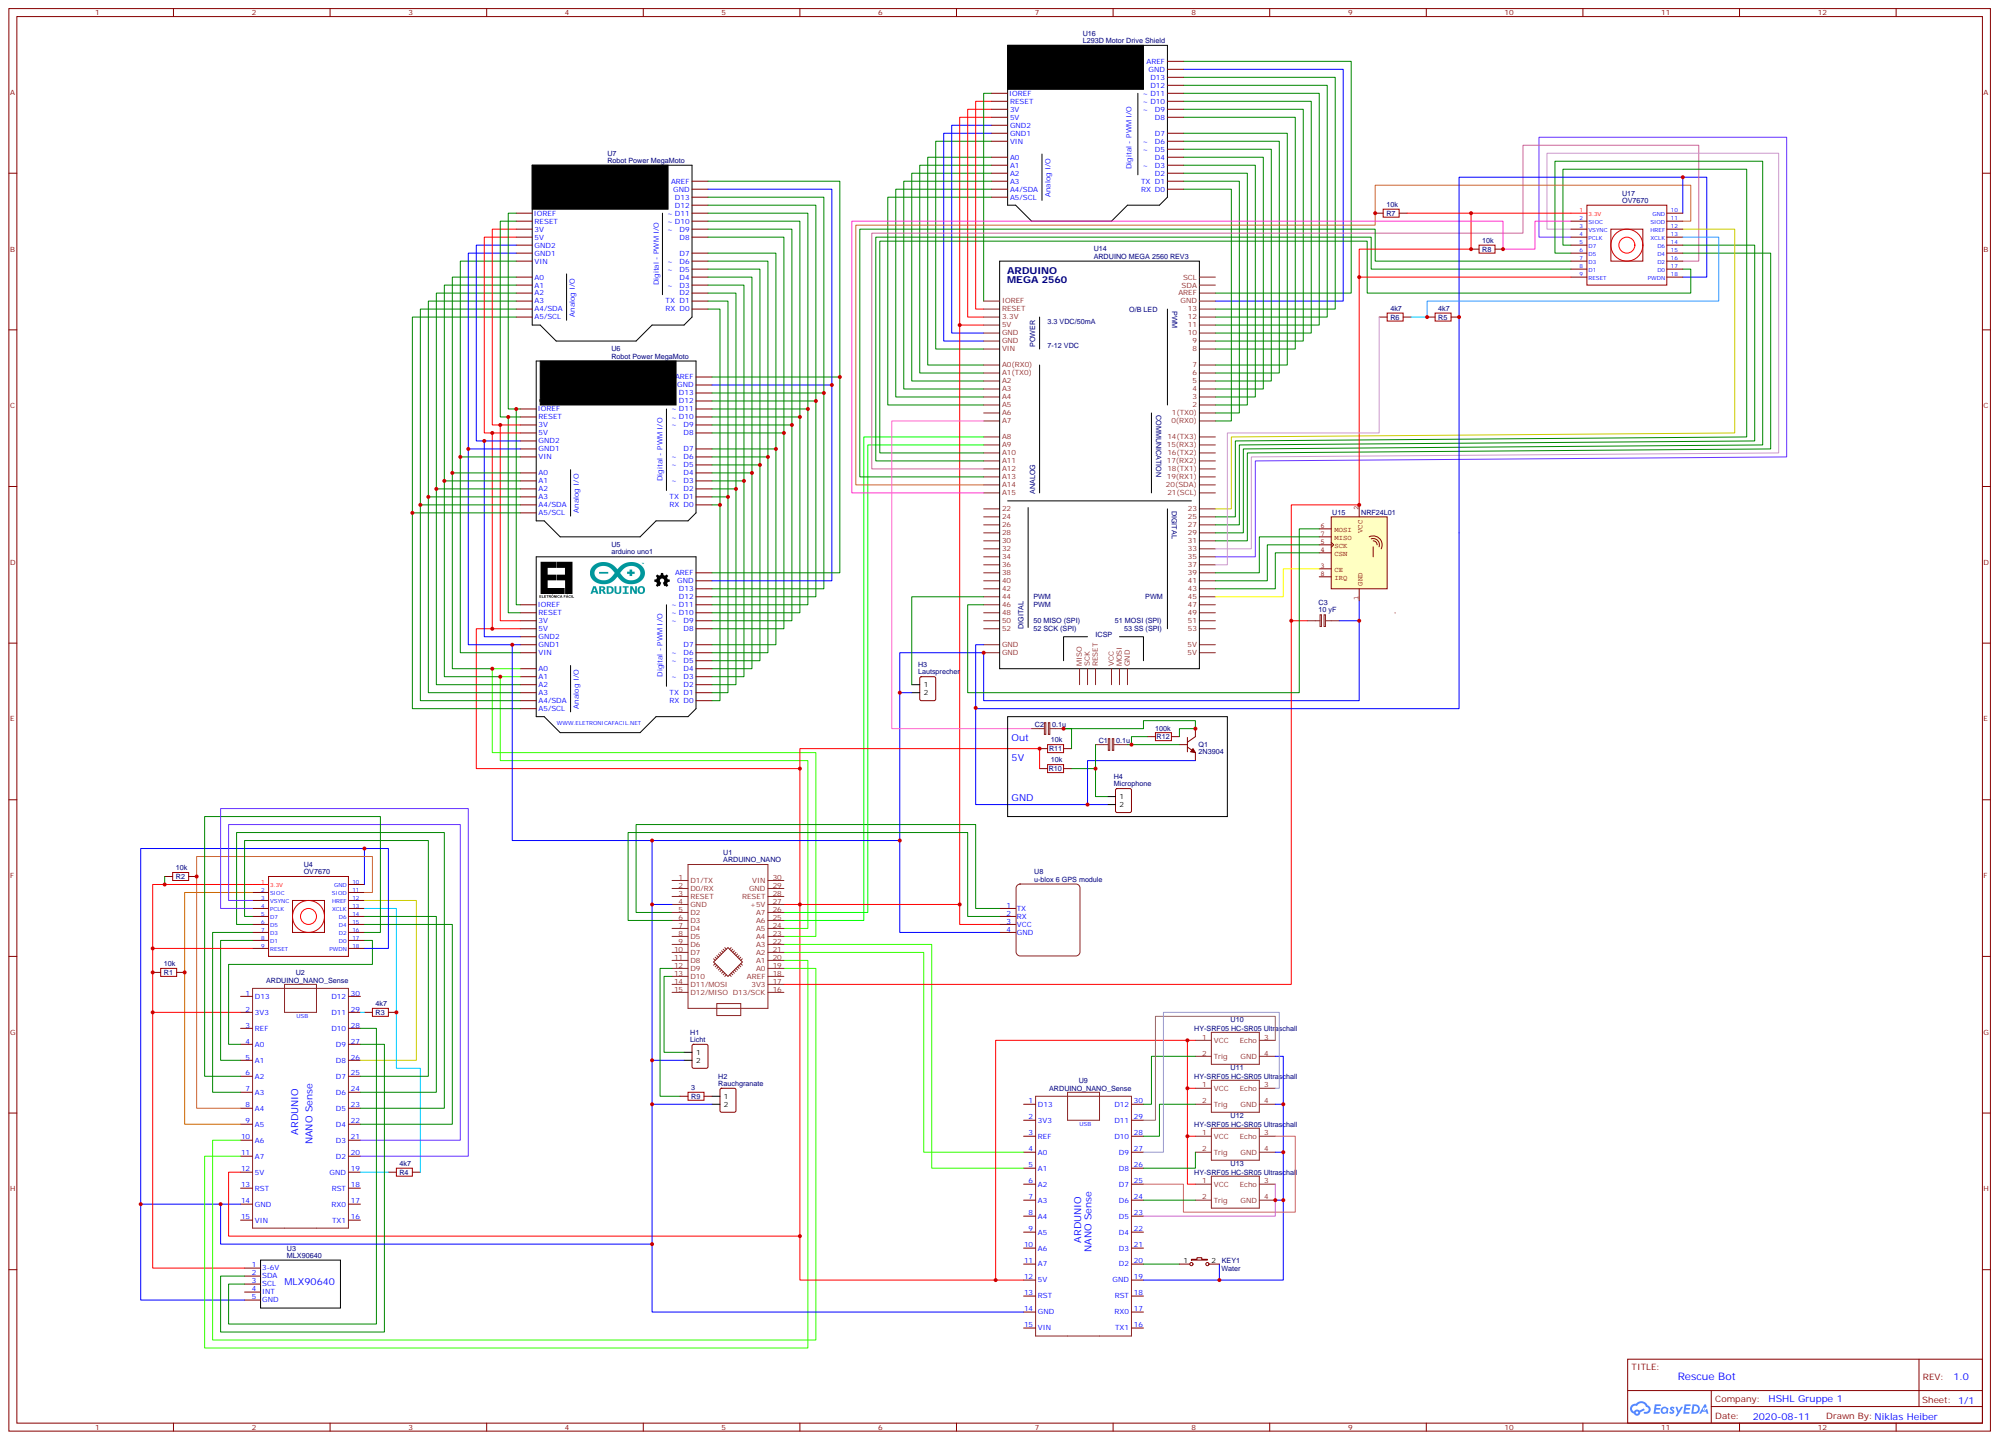
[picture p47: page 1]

USB ARDUNIO NANO Sense

## ARDUINO MEGA 2560

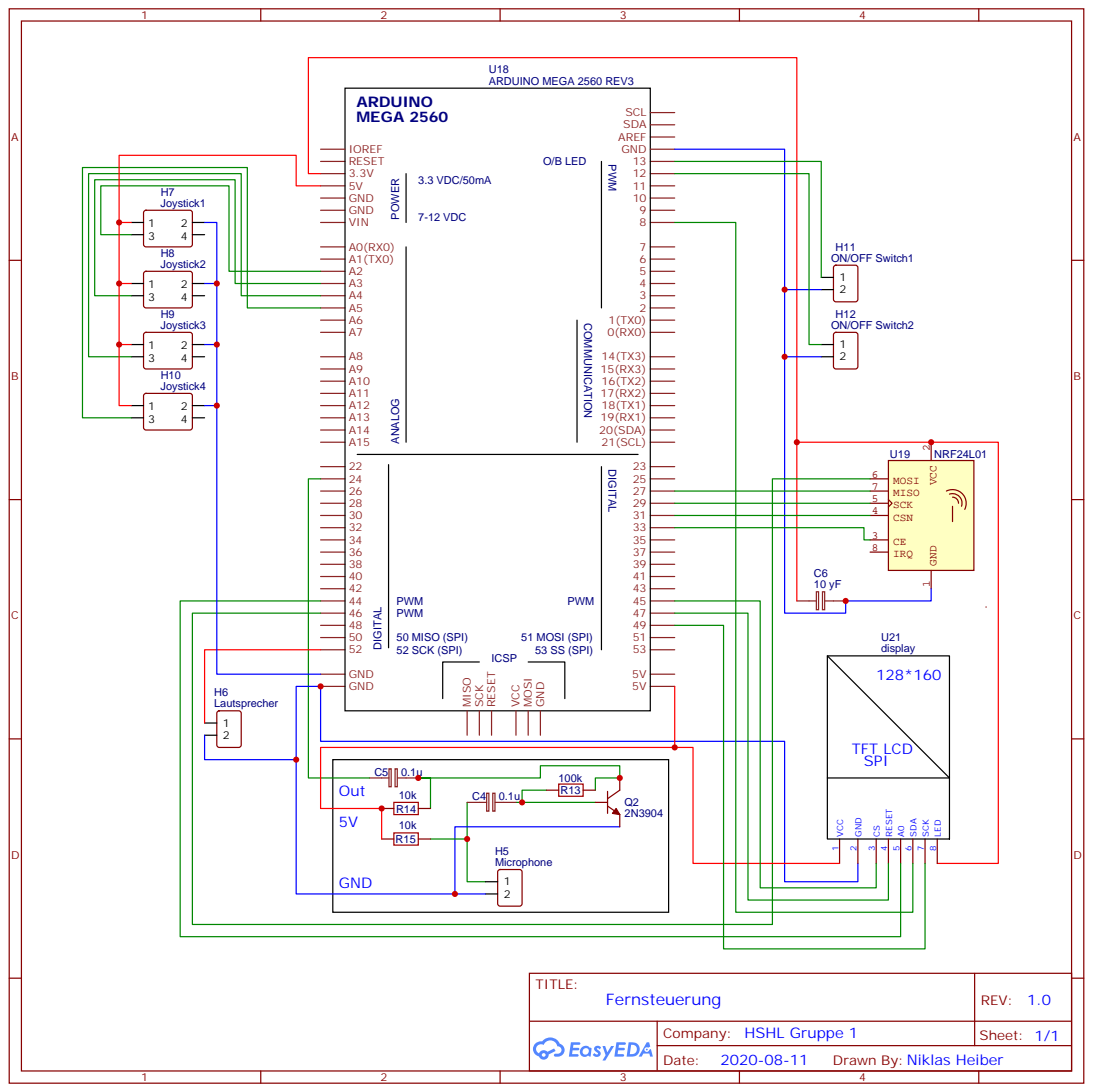
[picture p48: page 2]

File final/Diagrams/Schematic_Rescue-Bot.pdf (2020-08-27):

## ARDUINO MEGA 2560

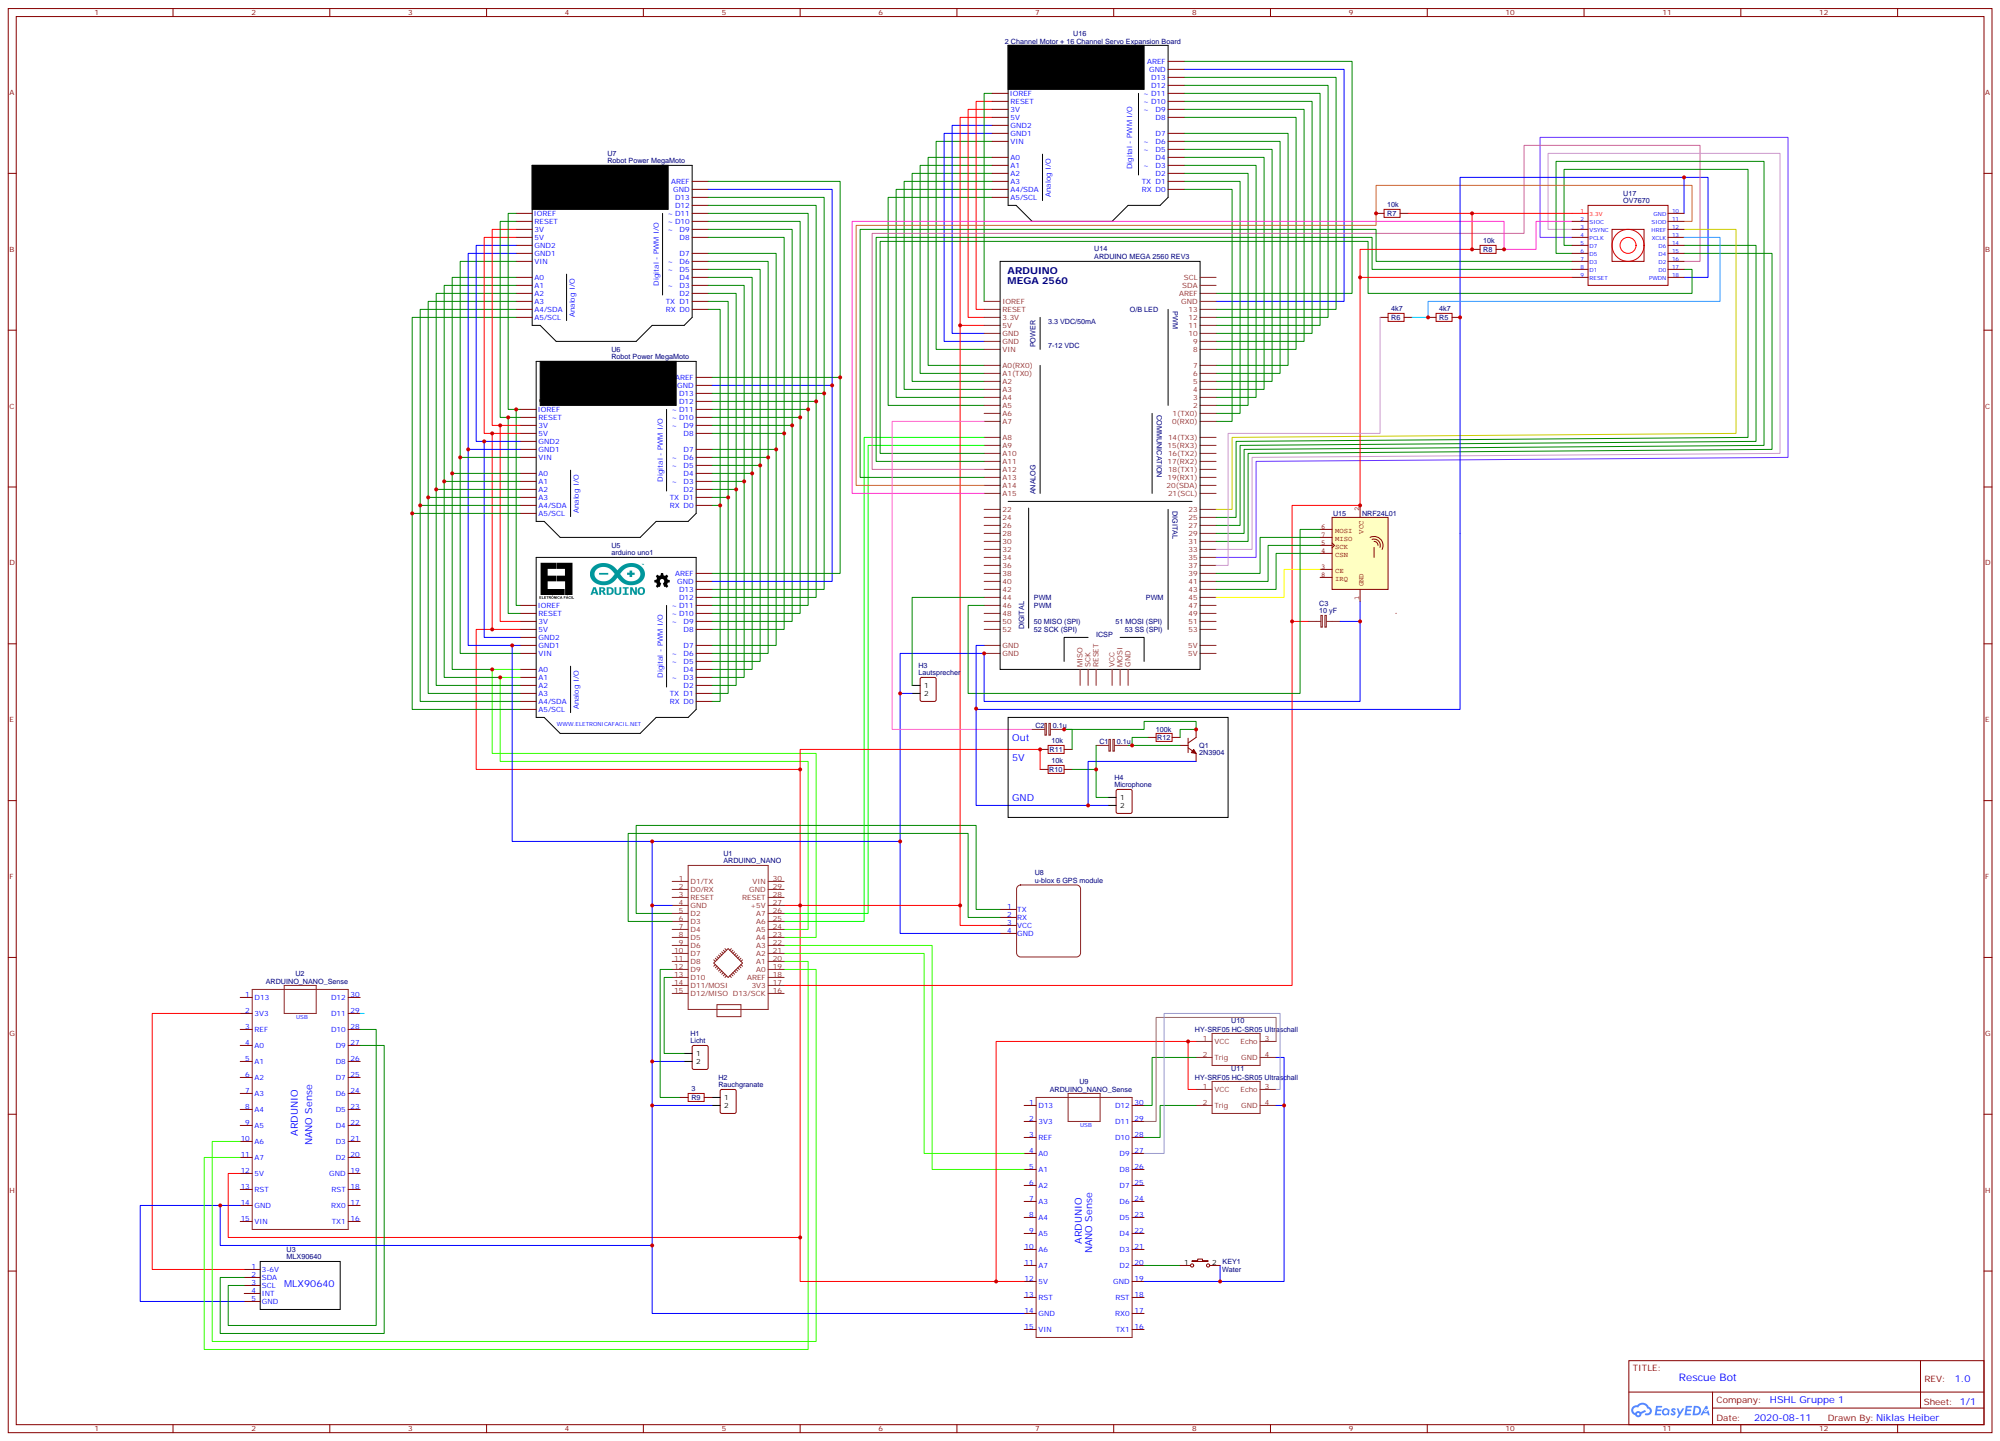
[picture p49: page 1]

2 Channel Motor + 16 Channel Servo Expansion Board

USB ARDUNIO NANO Sense

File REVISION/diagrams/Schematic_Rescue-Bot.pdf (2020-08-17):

## ARDUINO MEGA 2560

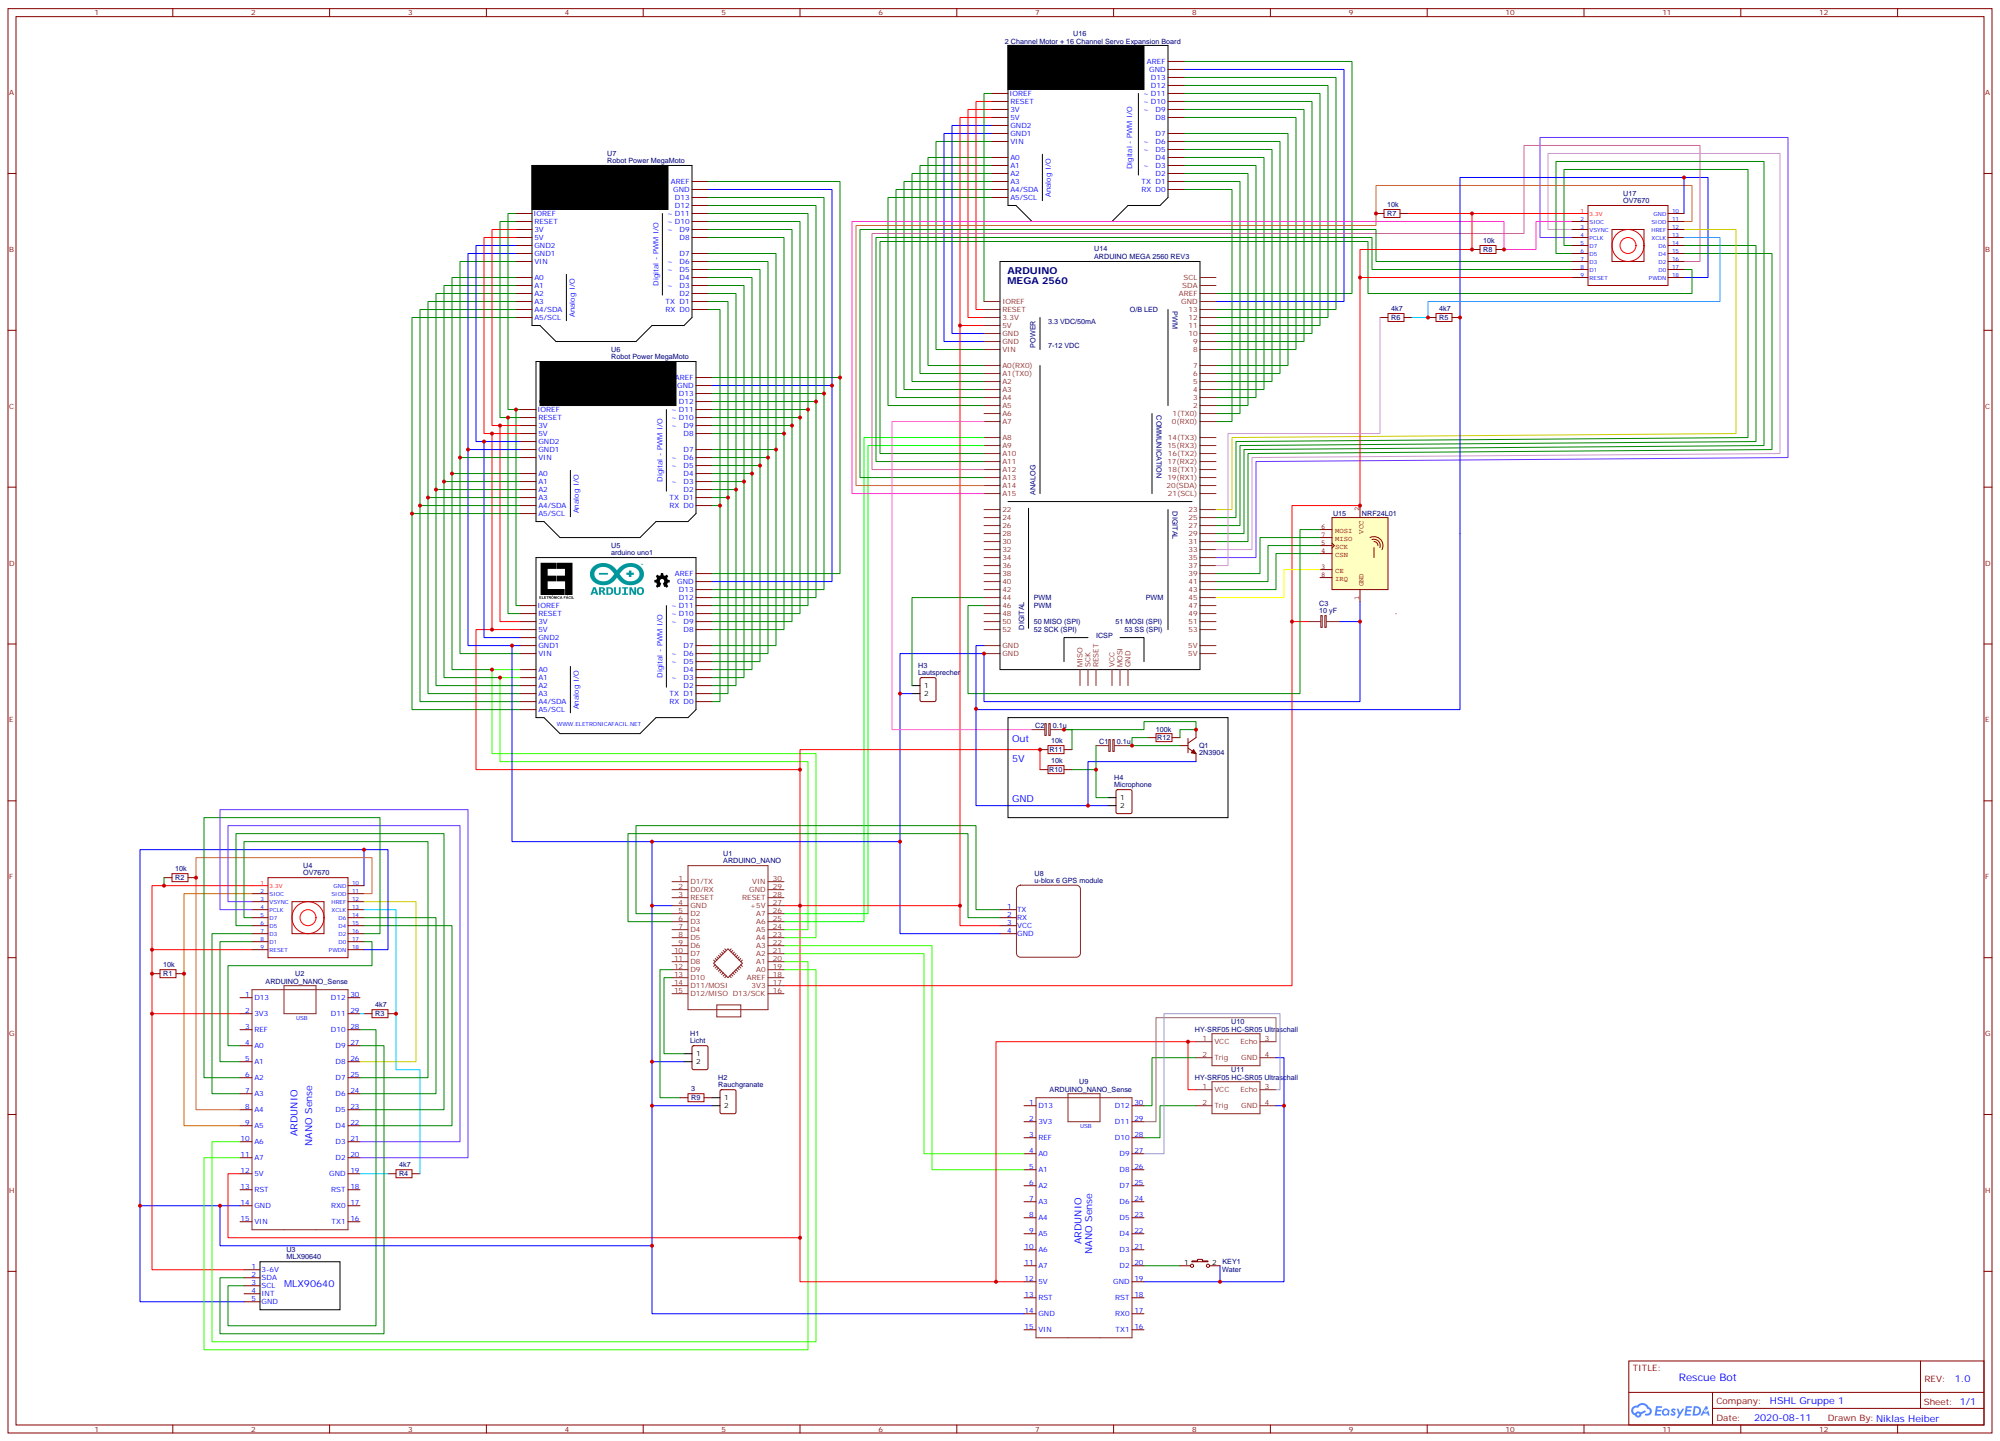
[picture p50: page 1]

2 Channel Motor + 16 Channel Servo Expansion Board

USB ARDUNIO NANO Sense

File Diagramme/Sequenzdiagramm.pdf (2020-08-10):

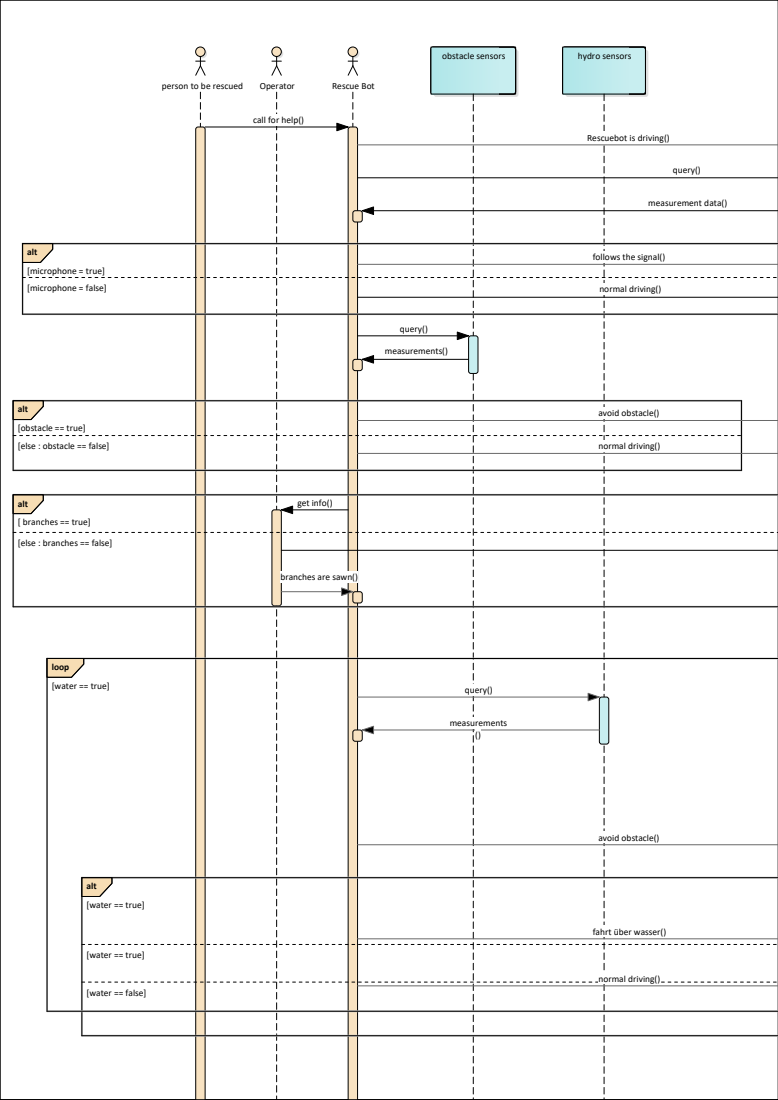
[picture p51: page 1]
Rescue Bot; obstacle sensors; hydro sensors; person to be rescued; Operator; alt; [water == true]; [water == false]; [microphone = true] [microphone = false]; loop; query(); normal driving(); measurement data(); get info(); measurements (); avoid obstacle(); measurements()

call for help()

Rescuebot is driving()

follows the signal()

alt
[obstacle == true]
[else : obstacle == false]

[ branches == true]
[else : branches == false]

branches are sawn()

fahrt über wasser()

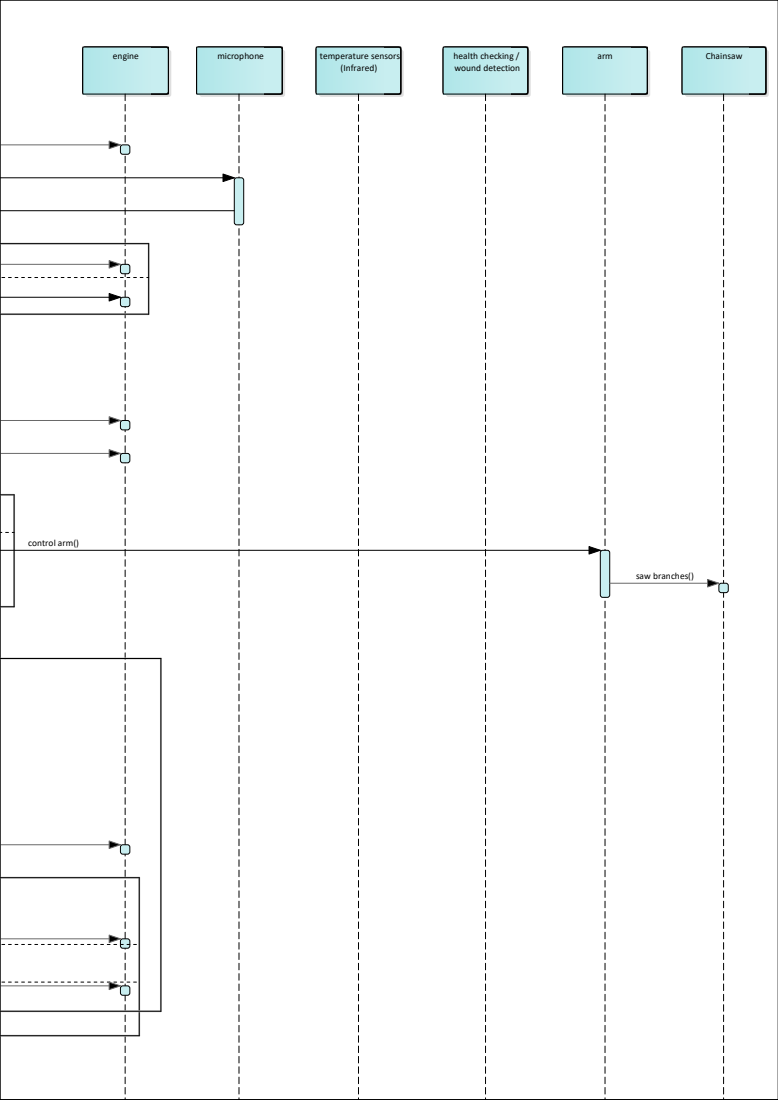
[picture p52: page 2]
engine; microphone; temperature sensors; (Infrared); health checking / wound detection; arm; Chainsaw; saw branches(); control arm()

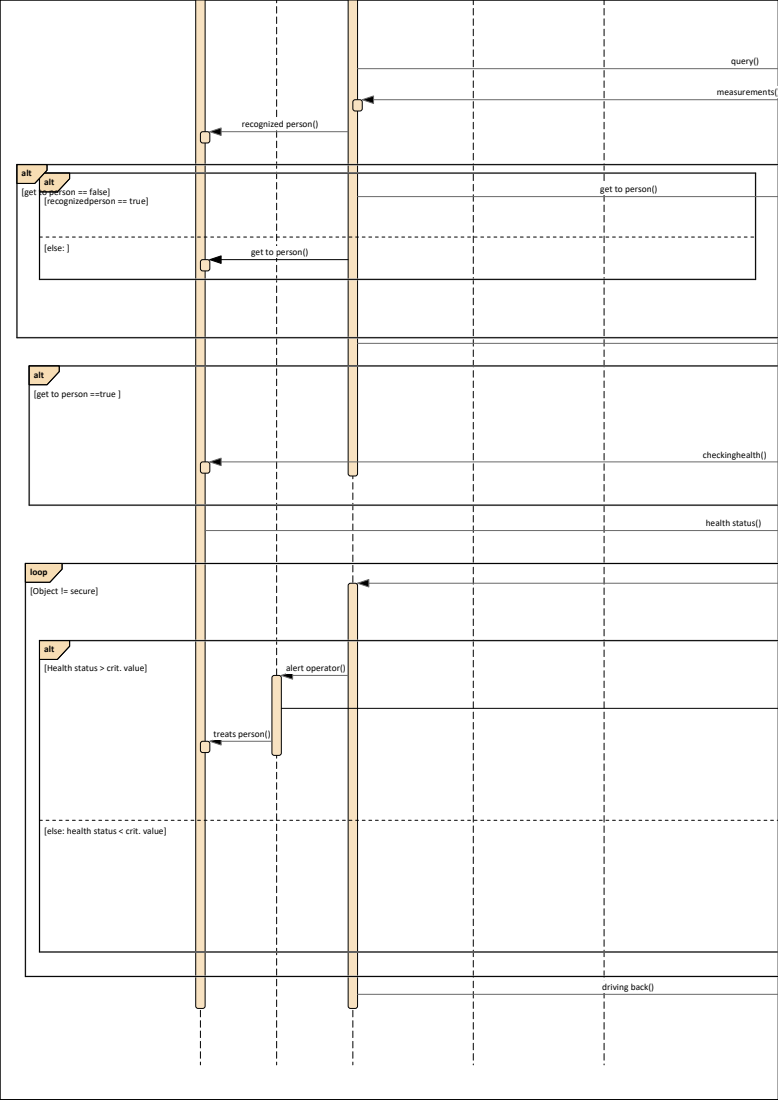
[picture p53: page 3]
loop; [Object != secure]; [else: ]; health status(); driving back(); measurements(); recognized person(); query(); treats person(); checkinghealth(); alert operator()

alt
[get to person == false]
[recognizedperson == true]

get to person()

[get to person ==true ]

[Health status > crit. value]

[else: health status < crit. value]

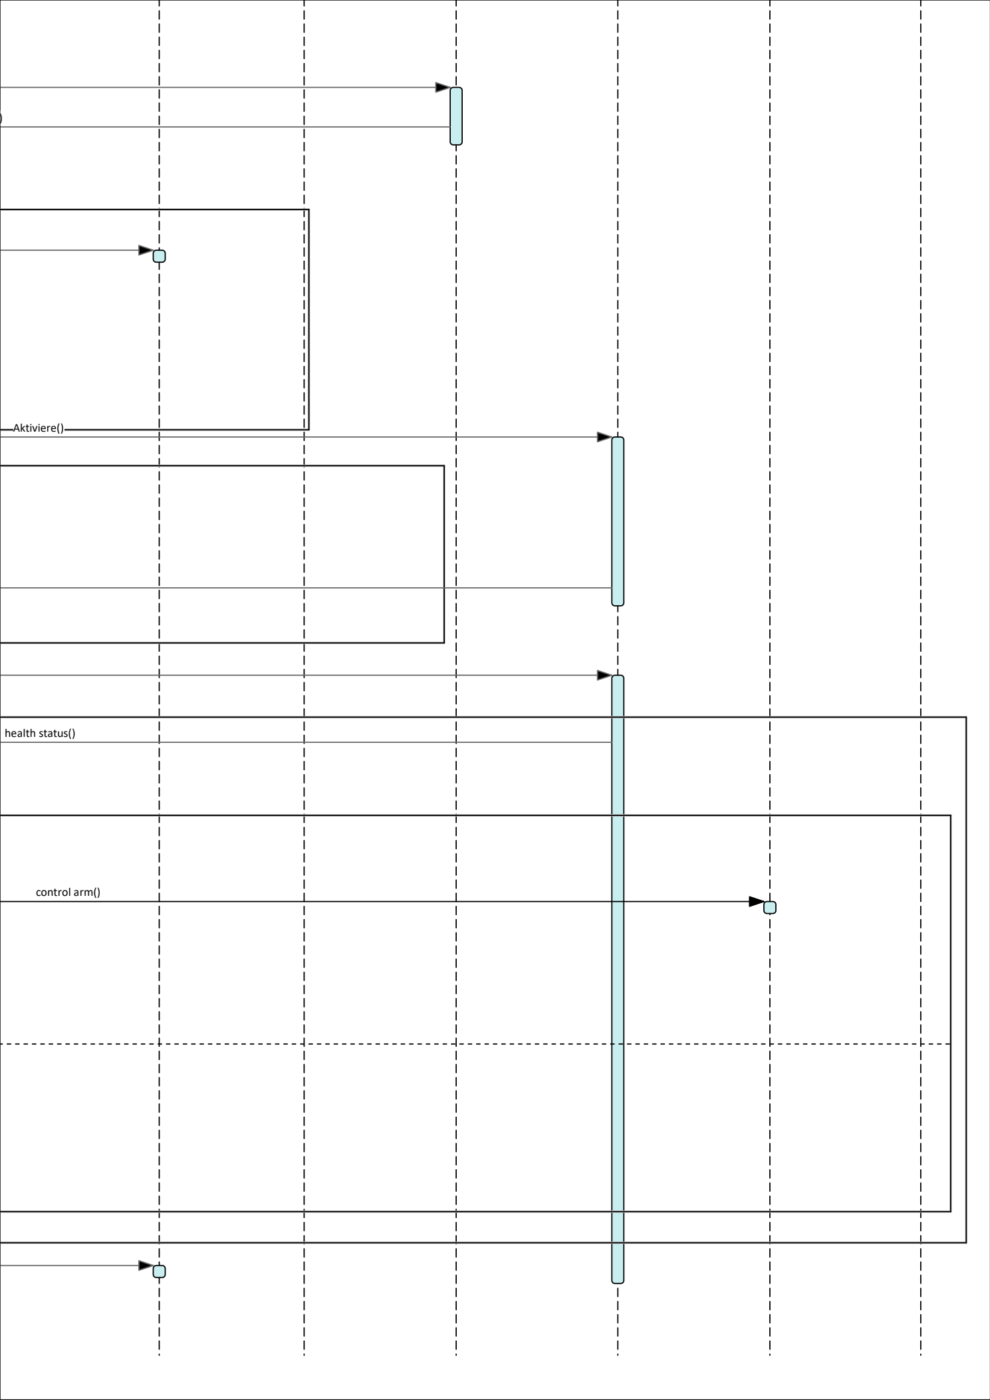
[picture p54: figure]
health status(); Aktiviere(); control arm()

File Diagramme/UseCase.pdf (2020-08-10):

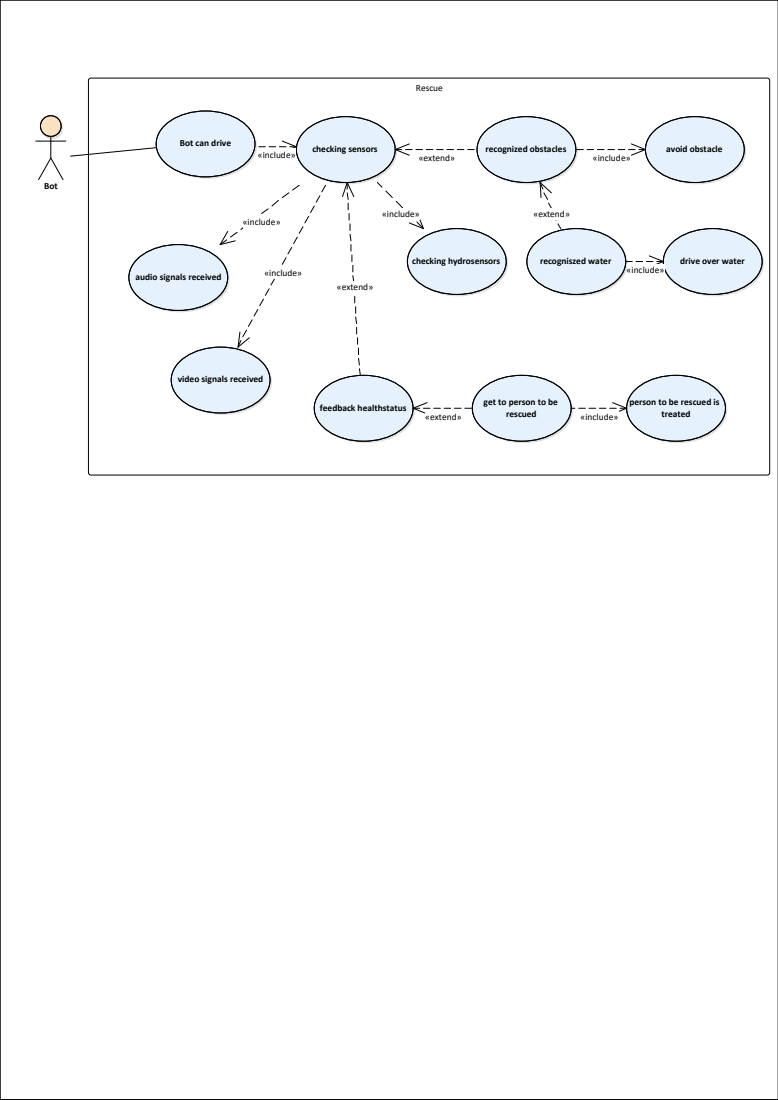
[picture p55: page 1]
Rescue; feedback healthstatus; Bot; avoid obstacle; recogniszed water; drive over water; checking hydrosensors; checking sensors; recognized obstacles Bot can drive; «include»; «extend»

audio signals received

video signals received

get to person to be
rescued

person to be rescued is
treated

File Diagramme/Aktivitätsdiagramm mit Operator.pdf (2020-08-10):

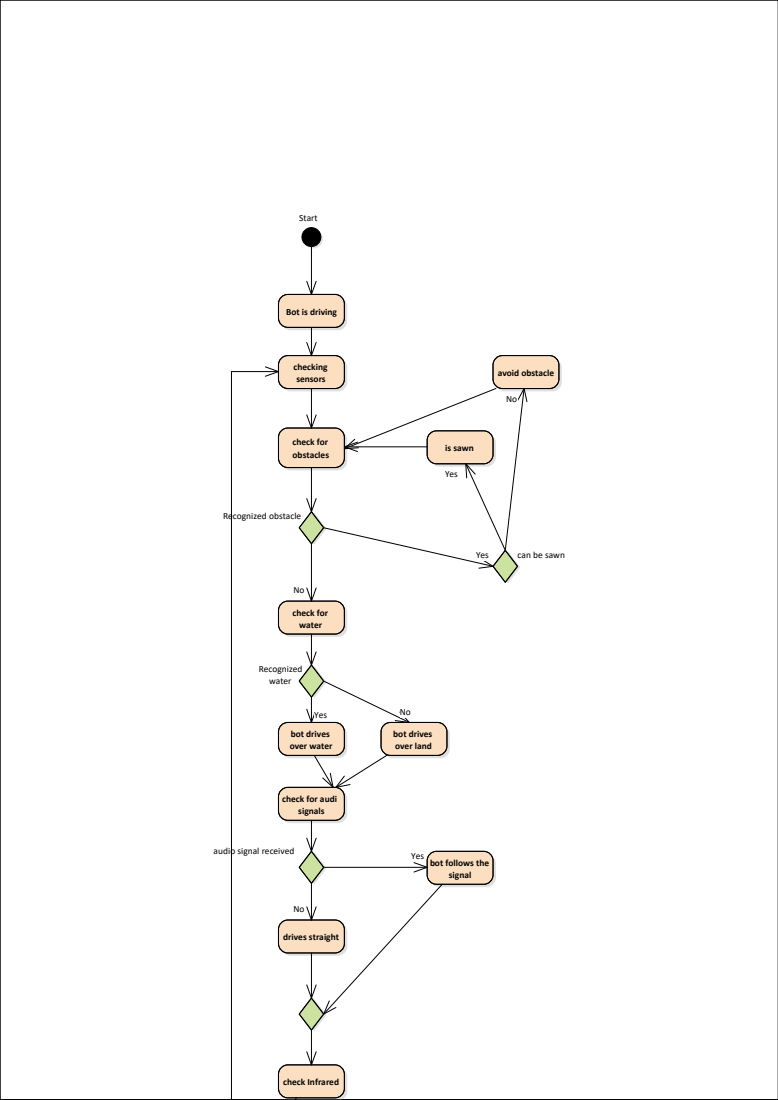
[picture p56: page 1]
Start; checking sensors; check for obstacles; Recognized obstacle; avoid obstacle; check for water; Recognized water; bot drives over water; drives straight; check Infrared; bot drives over land; is sawn; Yes

Bot is driving

can be sawn

check for audi
signals

audio signal received

Yes
bot follows the
signal

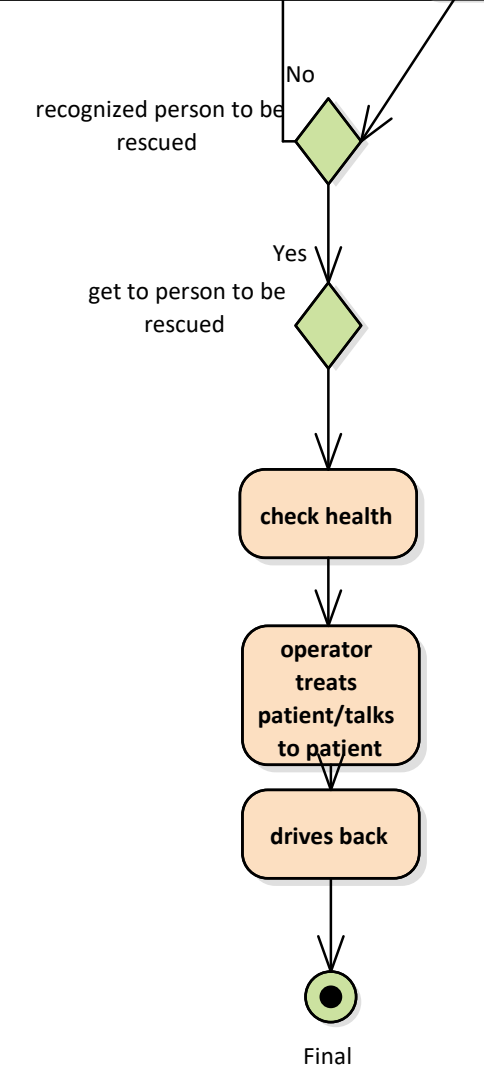
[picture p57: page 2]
Final; drives back; operator treats patient/talks to patient; check health; Yes

recognized person to be
rescued

get to person to be

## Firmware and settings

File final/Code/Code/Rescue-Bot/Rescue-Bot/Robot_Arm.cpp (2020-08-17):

#include <iostream>
#include <Adafruit_PWMServoDriver.h>

using namespace std;
#define MrPin1 = D1;
#define MrPin2 = D2;
#define M1Pin1 = D3;
#define M1Pin2 = D4;
#define M2Pin1 = D5;
#define M2Pin2 = D6;
#define M3Pin1 = D7;
#define M3Pin2 = D8;
#define SERVOMIN  150 // This is the 'minimum' pulse length count (out of 4096)
#define SERVOMAX  600 // This is the 'maximum' pulse length count (out of 4096)
#define USMIN  600 // This is the rounded 'minimum' microsecond length based on the minimum pulse of 150
#define USMAX  2400 // This is the rounded 'maximum' microsecond length based on the maximum pulse of 600
#define SERVO_FREQ 50 // Analog servos run at ~50 Hz updates

uint16_t Mr, M1, M2, M3; //Servos
uint8_t m0 = 0;
uint8_t m1 = 1;
uint8_t m2 = 2;
uint8_t m3 = 3;
float nump7, nump9, nump4, nump6, nump2, nump8, nump1, nump3; //Key inputs
int main()
{
    pwm.begin();
    pwm.setOscillatorFrequency(27000000);
    pwm.setPWMFreq(SERVO_FREQ);  // Analog servos run at ~50 Hz updates
    Mrotate = 0;    //Set servos to start position
    M1 = 4;
    M2 = 4;
    M3 = 4;
    uint16_t pulselen = SERVOMIN
    
   while(1){ //Loop forever || or remove loop and call this
       if(nump7 != 0 && nump9 != 0){
           if(nump7 != 0 && nump9 == 0 && Mr >= 2){
               Mr = Mr - pulselen;
               pwm.setPWM(m0, 0, Mr);
           }
           if(nump7 == 0 && nump9 != 0 && Mr <= 178){
               Mr = Mr +pulselen;
               pwm.setPWM(m0, 0, Mr);
           }
       }
       if(nump4 != 0 && nump6 != 0){
           if(nump4 != 0 && nump6 == 0 && M1 >= 10){
               M1 = M1 -pulselen;
               pwm.setPWM(m1, 0, Mr);
           }
           if(nump4 == 0 && nump6 != 0 && M1 <= 170){
               M1 = M1 +pulselen;
               pwm.setPWM(m1, 0, Mr);
           }
       }
       if(nump2 != 0 && nump8 != 0){
           if(nump2 != 0 && nump8 == 0 && M2 >= 10){
               M2 = M2 -pulselen;
               pwm.setPWM(m2, 0, Mr);
           }
           if(nump2 == 0 && nump8 != 0 && M2 <= 170){
               M2 = M2 +pulselen;
               pwm.setPWM(m3, 0, Mr);
           }
       }
       if(nump1 != 0 && nump3 != 0){
           if(nump7 != 0 && nump9 == 0 && M3 >= 10){
               M3 = M3 -pulselen;
               pwm.setPWM(m3, 0, Mr);
           }
           if(nump1 == 0 && nump3 != 0 && M3 <= 170){
               M3 = M3 +pulselen;
               pwm.setPWM(m3, 0, Mr);
           }
       }
   }
   
   return 0;
}

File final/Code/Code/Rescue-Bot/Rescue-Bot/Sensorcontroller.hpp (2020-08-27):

#pragma once
#include <iostream>
#include "../Interface_Sensors.cpp"

using namespace std;

class SensorController
{

#define ultrasonicPin1 29
#define ultrasonicPin2 27
#define ultrasonicPin3 25
#define ultrasonicPin4 23
#define pinMicrofone 22

#define watersens 20
#define sleep

private:
	float x1, y1, z1;	//Gyroscope
	float x2, y2, z2;	//compass
	float x3, y3, z3;	//acceleration
	float orientationToNorth;
	float orientation;
	int ultrasonicVL; int ultrasonicVR;
	int freqTow = 0; //frequenz für türme

	

	bool water;
	int obstacle[2];

	int readWater(int);
	int readUltrasonic(int);
	float readMagneticField(float , float , float );
	float readGyroscope(float, float, float);

	Ultraa Ula;
	Ultrab Ulb;
	Compass cmp;

public:
	char* checkForAudioSignals();
	float compass();
	float gyroscope();
	float acceleration();
	int* checkForObjects();
	int checkWater();
	char cameraMeasurement();

};
#include "Sensorcontroller.hpp"
int SensorController::readWater(int wert)
{
	return wert;
}
int SensorController::readUltrasonic(int wert)
{

	int temp = 0;
	switch (wert)
	{
	case 29:  return Ula.getSensor();
		break;
	case 27: return Ulb.getSensor();
		break;
	default: return 0;
		break;
	}
}
float SensorController::readMagneticField(float wert1, float wert2, float wert3)
{
	return wert1, wert2, wert3;
}
float SensorController::readGyroscope(float wert1, float wert2, float wert3)
{
	return wert1, wert2, wert3;
}
char* SensorController::checkForAudioSignals()
{
	Audio Aud;
	char audioData[4] = { '0','0','0','0' };
	//AudioOne{1,1,1,0,0,0,0,0,1} northwest
	//AudioTwo{1,1,1,0,0,0,0,1,0}northeast
	//AudioThree{1,1,1,0,0,0,0,1,1} northeast
	//Audiofour{1,1,1,0,0,0,1,0,0} Southeast shortway
	for (size_t i = 1; i < 5; i++)
	{	
		Aud.setturm(i);
		string audioSigna = "";
		 audioSigna = Aud.getSensorarray().c_str();
		//cout << audioSigna;	

		if (memcmp(audioSigna.c_str(), "1,1,1,0,0,0,0,0,1", 15) == 0)
		{
			audioData[0] = '1';
		}
		else if (memcmp (audioSigna.c_str(), "1,1,1,0,0,0,0,1,0", 15) == 0)
		{
			audioData[1] = '1';
		}
		else if (memcmp(audioSigna.c_str(), "1,1,1,0,0,0,0,1,1", 15) == 0)
		{
			audioData[2] = '1';
		}
		else if (memcmp(audioSigna.c_str(),"1,1,1,0,0,0,1,0,0", 15) == 0)
		{
			audioData[3] = '1';
		}
		else if (memcmp(audioSigna.c_str(), "1,1,1,0,0,0,1,1,0", 15) == 0)
		{
			//cout << "fehler: Keine Audio Codierung empfangen!";

		}
		else
		{
			//cout << "Allgemeiner fehler in der AudioNavigation!";
		}
	}
	/*
	if (audioSignals{1, 1, 1, 0, 0, 0, 0, 0, 1} || audioSignals{1, 1, 1, 0, 0, 0, 0, 1, 0} || audioSignals{1, 1, 1, 0, 0, 0, 0, 1, 1} || audioSignals{1, 1, 1, 0, 0, 0, 1, 0, 0})
	{
		switch (audioSignals)
		{
		case {1, 1, 1, 0, 0, 0, 0, 0, 1}: audioData[0] = true;
			break;
		case {1, 1, 1, 0, 0, 0, 0, 1, 0}: audioData[1] = true;
			break;
		case {1, 1, 1, 0, 0, 0, 0, 1, 1}: audioData[2] = true;
			break;
		case {1, 1, 1, 0, 0, 0, 1, 0, 0}: audioData[3] = true;
			break;

	}}*/

	cout << "\n";
	cout << audioData << endl;
	return audioData;
}

float SensorController::gyroscope()
{
	orientation = readGyroscope(x1, y1, z1);

	return orientation;
}

float SensorController::compass()
{
	orientationToNorth = cmp.getCompass();

	return orientationToNorth;
}


int* SensorController::checkForObjects()
{
	int temp[2] = { 0, 0};
	 temp[0] = readUltrasonic(ultrasonicPin1);
	 temp[1] = readUltrasonic(ultrasonicPin2);
	
	 return temp;
}

int SensorController::checkWater()
{
	Wasser water;
	int waterdata = water.getSensor();

	return waterdata;
}

char SensorController::cameraMeasurement()
{
	char msg = 'n';
	return msg;
}

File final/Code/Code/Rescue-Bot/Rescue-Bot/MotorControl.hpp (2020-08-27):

#pragma once
#include <Windows.h>
#include "../Interface_Sensors.cpp"
class MotorControl
{
#define enginePin1  3
#define enginePin2  4
#define directionPin1  5
#define directionPin2  6
#define degreePerSecond  3

#define delay  
#define analogWrite 

public:
	void acclerator(int direction);
	void rotation(int angle, int orientation);
	MotorControl(DriveMode _drvMode);
	MotorControl();
private:
	void engine(int engine1, int engine2);
	DriveMode drvMode;
	Move Mov;

};
MotorControl::MotorControl()
{
}
MotorControl::MotorControl(DriveMode _drvMode)
{
	drvMode = _drvMode;
}
	
void MotorControl::engine(int engine1, int engine2)		//Engine1 = right Engine2 = left
{
	cout << endl << "Ausrichtung: "<< Test.orientation << endl;
	if (engine1 == 100)
	{
		Mov.movestraight(enginePin1,255, 255);

	}
	else if (engine1 == 0)
	{

		Mov.movestraight(enginePin1,255, 0);
		

	}
	else if (engine1 == 200)
	{
		Mov.movestraight(enginePin1,0, 255);

	}

	{
		if (engine2 == 100)
		{
			Mov.movestraight(enginePin2,255, 255);

		}
		else if (engine2 == 0)
		{
			Mov.movestraight(enginePin2,255, 0);
		}
		else if (engine2 == 200)
		{
			Mov.movestraight(enginePin2,0, 255);
		}
	}
}
void MotorControl::acclerator(int direction)
{
	switch (direction)
	{

	case 0: 	if (drvMode.getDriveMode() == 0) //0 = water
	{
		engine(0, 0);
	}
		  else
	{
		engine(50, 50);
		Sleep(100);
	}
		  break;
	case 1: engine(100, 100);
		break;
	case 2: engine(200, 200);
		break;
	default:
		if (drvMode.getDriveMode() == 0) //0 = water
		{
			engine(0, 0);
		}
		else
		{
			engine(50, 50);
			Sleep(100);
		}
		break;
	}
}
void setOrientation(int orientation)
{
	SetOrientation SOR;
	switch (orientation)
	{
	case 0:SOR.setori('N');
		break;
	case 90: SOR.setori('E');
		break;
	case 180:SOR.setori('S');
		break;
	case 270:SOR.setori('W');
		break;
	}
}
void MotorControl::rotation(int angle, int orientation)
{	


	setOrientation(orientation);
	int absangle = abs(angle);
	if (absangle <= 180 || angle > 0)
	{
		int secondsToRotate = absangle / degreePerSecond;
		size_t i = secondsToRotate;
		for (i; i > 0; i--)
		{

			//engine(200, 100);
			delay(1000);    //spezifisch für arduino 
		}
		//engine(0, 0);
	}
	else if (absangle > 180 || angle < 0)
	{
		int secondsToRotate = (360 - absangle) / degreePerSecond;
		for (size_t i = secondsToRotate; i > 0; i--)
		{
			//engine(100, 200);
			delay(1000);    //spezifisch für arduino 
		}
		//engine(0, 0);
	}

}

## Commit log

2020-07-13 gantt diagramm erstellt
    meilensteine eingetragen. arbeistpakete müssen noch erstellt werden
    [gantt.xlsx]
2020-07-16 Update gantt.xlsx
    Aufgaben bis zum ersten Meilenstein eingetragen
    [gantt.xlsx]
2020-07-19 Create Activity Diagram
    Ordner "Diagramme " erstellt
    Enterprise Architect "Rescue-Bot " erstellt
    Aktivitätsdiagramm auf grundlage des Use-Case Diagramms erstellt
2020-07-20 Update: gantt & resque- bot.eapx
    [gantt.xlsx]
2020-07-20 Add: Stakeholder AND print diagrams
2020-07-23 Class Diagram: Create first prototype
    Angefangen mit dem Klassendiagram
2020-08-03 größere paddel
    [belt2.SLDPRT, gantt.xlsx, rescue_bot_prototype2.SLDASM]
2020-08-03 first sketch of sw impl.
    create State-machines of:
    audio navigation
    gear changing
2020-08-08 print pdf Aktivitäts Diagramm
2020-08-08 Update print pdf
2020-08-08 Update Diagrams & PDF Prints
2020-08-08 Upload Powerpoint
2020-08-10 Roboter Arm
    [Arm_unten.SLDPRT, Roboter_arm_v1.SLDASM, arm_oben.SLDPRT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]
2020-08-10 update Use-Case, Sequenz Upload picture for presentation
2020-08-10 Rescue bot mit arm und säge
    [Roboter_arm_v1.SLDASM, arm_oben.SLDPRT, baugruppe_säge.SLDASM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]
2020-08-10 Create map_array.txt
    test ground array
2020-08-10 ultrasonic sensors placed
    [Roboter_arm_v1.SLDASM, Ultraschallsensor.SLDPRT, baugruppe_säge.SLDASM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]
2020-08-11 Update SensorCheck_Pseudo
2020-08-11 battery added
    added removable battery
    [Akku.SLDPRT, baugruppe_säge.SLDASM, body.SLDPRT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]
2020-08-11 microphone added
    microphone for orientation
    [body.SLDPRT, microphone.SLDPRT, microphone_adapter.SLDPRT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]
2020-08-11 medikit added
    [Roboter_arm_v1.SLDASM, baugruppe_säge.SLDASM, kette.SLDPRT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]
2020-08-11 technische zeichung
    [rescue_bot_prototype2.SLDASM, rescue_bot_technische_zeichung.SLDDRW]
2020-08-12 gesamthöhe hinzugefügt
    [rescue_bot_technische_zeichung.SLDDRW]
2020-08-14 new context diagram
    the hole project has to be revised from scratch.
    The starting point for this is the context diagram.
2020-08-17 renewed robot arm
    [Arm_unten.SLDPRT, arm_oben.SLDPRT, baugruppe_säge.SLDASM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]
2020-08-17 Sensorcontroller.h systax korrekturen
2020-08-17 build and checke stl files
    [Arm_unten.SLDPRT, arm_oben.SLDPRT, arm_oben.STL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]
2020-08-21 Code-Tracebarkeit verbessert
2020-08-23 added motors, side paddles and beacon
    [AssemGear.SLDASM, AssemMotor.SLDASM, Baquela_Encoder.SLDPRT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]
2020-08-24 fehlerbehebung Motorcontrol
2020-08-24 final 3D model
    [0-605-21-01.SLDPRT, 0-605-21-02.SLDPRT, 0-605-21.SLDASM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]
2020-08-24 final 3d model with renderings
    [AssemGearfinal.SLDASM, AssemMotorfinal.SLDASM, Faulhaber_2342L012CRfinal.SLDASM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]
